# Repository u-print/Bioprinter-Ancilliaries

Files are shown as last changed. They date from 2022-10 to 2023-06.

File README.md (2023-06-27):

# Bioprinter-Ancilliaries
Contains various helper functions/files for the Bioprinter.

# List of Contents
- Simplify3D profile for different syringe sizes mounted on the E3D Toolchanger
- wellToPlate scripts - Input gcode file and duplicate to desired amount of wells in a multi-well plate
- WellPlateDispenser - Generate gcode for dispensing liquids into wells. Dispenses into wells based on starting and ending well, uses a serpentine pattern. Use even numbers of rows!

#Pre-requisite packages:
- Numpy
- OpenCV python
- Matplotlib

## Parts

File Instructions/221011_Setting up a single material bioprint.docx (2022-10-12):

Setting up a single material bioprint

- Things you need to setup a single material bioprint
  - Simplify3D
  - Slicing profile matching the syringe and needle used in the print
  - STL-file of the object to be printed
  - Python3 installed - https://www.python.org/downloads/release/python-3103/
1. Start Simplify3D, go to Tools → Options → Machine. Click on Add under “Printer model” and select the file suitable file for your plate insert. This will give you a view of how the print bed is looking and allows you to place the model in the well you wish to print in.
2. Import your STL into Simplify3D. The file will be dropped into the model of the print platform. Orient it appropriately, position the part in the well you want to print in.
3. Select the printing profile and adjust settings such as layer height, nozzle diameter. Make sure that your desired tool is selected in the “Extrusion”-tab of Simplify3D.
4. Generate the g-code file and export it.
5. The following procedure can be done in several ways. Since we are printing into a well, we need to make sure that the tool is located correctly in the XY-plane BEFORE moving to the Z=0 position.
  1. Place the g.code file you generated from Simplify3D in the same folder as the supplied python program. The executable file can be downloaded from U-PRINTs Github page. Run the program and follow the instruction in the terminal. it will generate a new g-code-file as well as a picture of what wells will be printed into. Upload the newly generated g-code file to Duet Web Control (DWC).
6. Upload you gcode file to DWC via the “Files”-tab.
7. Prepare your syringe with bioink and attach it to the tool you are planning to use. If the plunger of the syringe does not fit, go into DWC and run the macro “Tx – Select” and manually move the plunger until the syringe and syringe holder fits. Then run “Tx – Deselect”
8. Now that bioink is loaded and g-code uploaded, its time to tell the printer where to start.
9. Run “Tx – Pickup” and jog the needle to the well you are going to print in. Jog the Z-axis until the needle is sufficiently submerged in the support bath or placed appropriately above the surface you will print on.
10. Run the macro “Zero Z-axis”, followed by T-1 to leave the tool in its dock. Now the printer knows where to start, the only thing we need to do now is to prime the nozzle to make sure that bioink can be extruded.
11. Select the tool you are planning to use with the macro “Tx – Select” then jog the plunger until you see bioink leaving the needle. Deselect the tool with the macro “Tx – Deselect”
12. Now everything should be prepared. To start the print, go to “Jobs” and start the g-code you uploaded earlier.

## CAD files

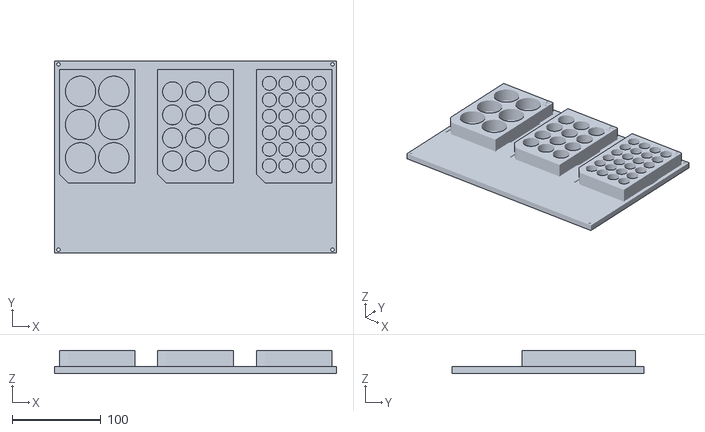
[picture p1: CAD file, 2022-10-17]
Simplify3D files/Simplify3D-6-12-24 well model.stl
318.0 x 217.0 x 26.2

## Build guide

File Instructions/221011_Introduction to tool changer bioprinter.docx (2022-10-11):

Instructions for tool changer bioprinter

To use the bioprinter, either running prints or writing macros for automation, it is necessary to understand the way that the bioprinter interpret instructions. The printer uses 4 stepper motors to control the axes of the bioprinter. 3 motors for XYZ and 1 motor for the tool changing mechanism. All movements and behaviors of the bioprinter is controlled by g-code. G-code can be entered manually, one string at a time, or by running a file containing several strings of g-code, which will be run sequentially. The files generated from a slicer is just a text document containing a sequence of g-code commands, controlling movements of all axes in the system. Below are some examples of how G-code is interpreted by the controller card. Text written after a “;” is ignored by the machine, and is present only for describing the action of the command.

Example 1:

G1 X100 F5000

This command will move the toolhead to the coordinate X100 with a speed of 5000 mm/min. No other axes will be moved since no other axes than X is specified.

Example 2:

G1 X100 Y100 F5000

This command will move the toolhead to coordinate X100 Y100 in a coordinated movement with a speed of 5000 mm/min.

Example 3:

G1 X100 F5000

G1 Y100 F5000

This set of commands will first move the toolhead to coordinate X100, followed by movement to Y-axis to coordinate Y100. These moves will be done after each other, and not in a coordinated manner as in example 2. Each movement will be done with a speed of 5000 mm/min.

At any point when the machine makes a movement, there is a g-code command being sent to the controller. No movement will be done randomly, so unexpected movements of the bioprinter is always caused by instructions given to the printer. This is good to keep in mind when troubleshooting erratic behavior. If it is doing something you don’t understand why, ask yourself the following:

- What sequence of commands can make the printer behave like this?
- Where could these commands be?
- What triggers these commands to be sent?

Starting up the bioprinter

1. Start the bioprinter on the switch (left backside)
2. Connect to the WiFi-hotspot created by the controller card.
  a. SSID: TC Bioprinter B3
  b. PW: 3D-prin7ing
3. Browse to 192.168.111.111 to reach the Duet Web Control. This is the interface you will use to control the bioprinter. Learn more about the interface here: https://docs.duet3d.com/User_manual/Reference/Duet_Web_Control_Manual

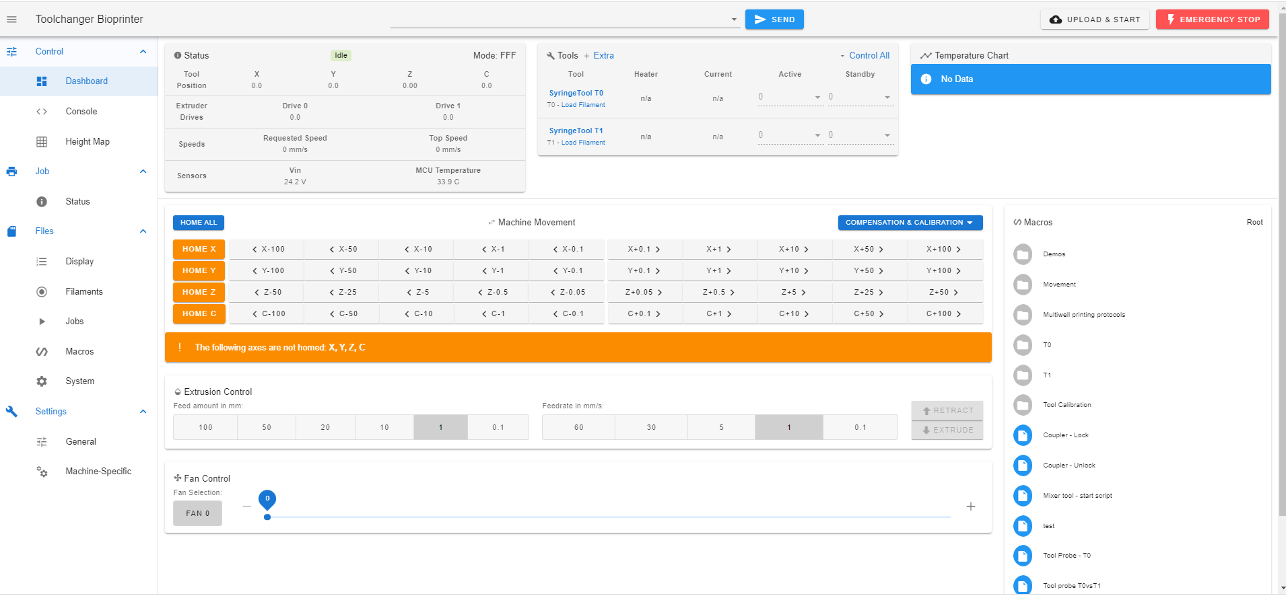
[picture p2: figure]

The motors used on this printer is “open loop”, meaning that motors do not provide information about the position in absolute terms. All movements are done in relation to a “home position”. All axes have a minimum position and a maximum position, and the “home position” is defined as the minimum position. This means that front left is the home position for the XY axes.

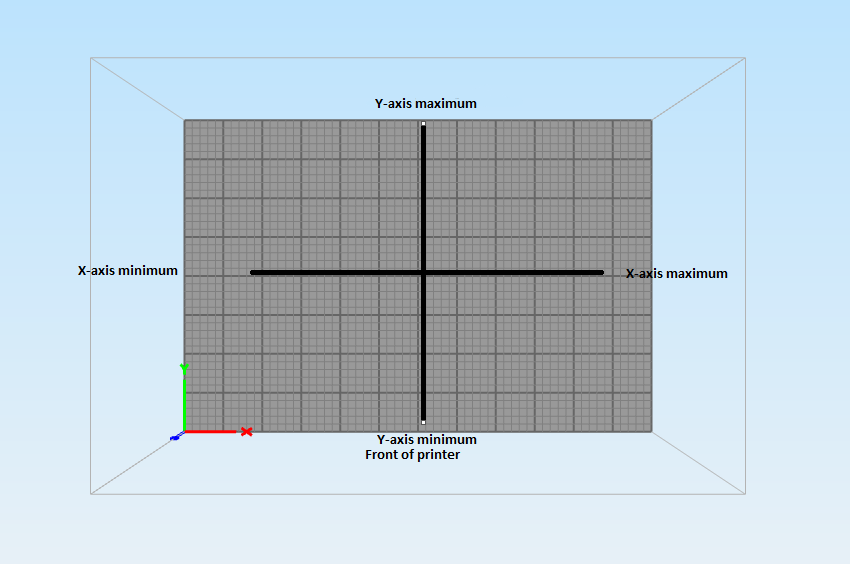
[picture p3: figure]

First step of using the bioprinter is making sure that the home position is correctly identified. This is done by running a g-code command for homing the axes.

The command for homing an axis is G28. Since we need all axes to find their homing position, their reference point, we need to home all axes. This can be done by manually sending the command G28 XYZC, or pressing the “Home all” button in DWC. The only thing this button does in sending that command to the g-code interpreter on the controlled card.

When your axes are homed, the buttons in DWC will turn blue, indicating that the axis limits are now known, and the printers coordinate system is established.

With the printer homed, lets explore what happens if we want to pick up a tool mounted in its tool dock. The tools are numbered from 0 to 3. The outer left tool is T0, the one right next to it is T1 etc. All text written after “;” is just comments to understand the command, and will not be interpreted by the controller card as instructions. The command for picking up a tool is:

T0 ; This command tells the printer to pick up T0. When this command is sent, it is triggering a macro containing a list of g-codes that involves all the movements of picking up the tool.

When a T-command is sent, lets say T0 in this example, the following happens.

1. A macro called t0pre is run. This macro contains the instructions for picking up T0. By modifying this macro, we can control the behavior from the point where the Tx command is sent until the tool is picked up.
2. Another macro called t0post is run. This macro is started when the tool is picked up and the g-code in t0pre is finished. By modifying this macro, we can control the behavior from the point where the tool is picked up. This could include priming of nozzles, wiping of excess bioink from the needle or positioning the toolhead appropriately.

The macro for leaving the tool in its dock is “T-1”. This will leave the selected tool in its dock.

When T-1 is sent, it calls a macro called t0free. This contains the instructions for leaving the tool in its dock.

All these macros can be found under the “system” tab in DWC. Take some time to look into these files to understand what is actually happening when the tool change commands are sent to the printer. There are a huge variety of g-code commands available, see website for more commands and parameters: https://docs.duet3d.com/

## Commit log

2022-10-11 Added introduction and instructions for single material bioprinting
2022-10-12 Updated instructions for single material bioprinting
2022-10-17 Create Syringe Tool - 1001 TLL - 0.6mm needle.fff
2022-10-17 Uploaded print-profiles and well plate insert models
    [Simplify3D-6-12-24 well model.stl]
2023-01-10 Create wellToPlate_230109.py
    Updated version of wellToPlate compatible with multi-material printing. New function insert_gcode inserts G1 R2 commands after each toolchange to ensure XY-movements is done before Z-movement
2023-01-30 Updated wellToPlate script and .exe
    Now allows for floats as distance between wells for 384 well plates.
2023-06-27 Create 230614_WellPlateDispenser_v4.py
    A script with a simple GUI to generate gcode for dispensing into multi well plates. Input should be the syringe size used, the amount to be extruded in each well, the pause in seconds after the extrusion, the number of wells to print in in each row, and the Z-lift after extrusion before moving to the next well.
    Does not work well for uneven numbers of rows.
